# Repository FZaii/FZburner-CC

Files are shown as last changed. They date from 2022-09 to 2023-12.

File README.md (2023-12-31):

<p align="center">
  <a href="https://space.bilibili.com/1898517">
    
  </a>
    <br />
</p>

<h1 align="center">FZburner For CC</h1>

*<p align="center">给大鱼CC 3D打印机设计的一款打印头
  <br />
  [A burner for the DaYu CC 3D parinter]</p>*

**<p align="center">**
**<h3 align="center">最终版（v1.61）STEP及STL文件已上传！</h3>**
**<h3 align="center">✨[FZburner Mk2 已发布！！](https://github.com/FZaii/FZburner)✨</h3>**
*<p align="center">反馈意见可以通过[📺BiliBili](https://space.bilibili.com/1898517)私信</p>*

 ---
 
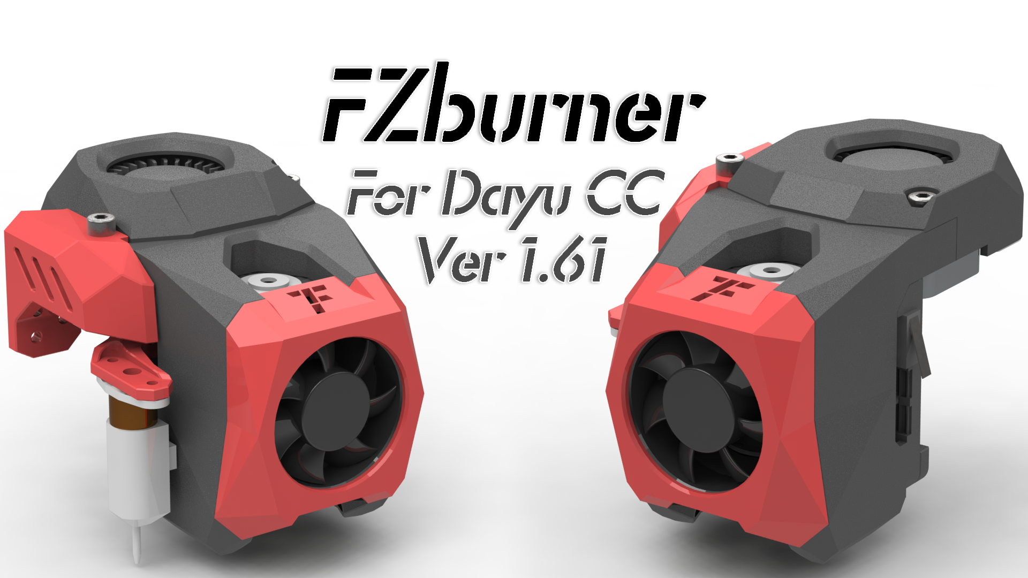
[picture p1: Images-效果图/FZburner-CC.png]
FZburner-CC

 
 ---

 ## 目录
 
- [功能特色](#功能特色)
- [更新历史](#更新历史)
- [实机照片](#实机照片)

 ---
  
### 功能特色
> - [x] 远程挤出（近程挤出可选用[**Sherpa Mini挤出机**](https://github.com/Annex-Engineering/Sherpa_Mini-Extruder)或者[**FZ挤出机**](https://github.com/FZaii/FZ-Extruder)等固定孔位间距为43.5mm的挤出机）
> - [x] E3D V6 热端
> - [x] 4010 热端风扇
> - [x] 4020 / 5015 物料风扇
> - [x] BLTouch 安装位
> - [x] [**Klicky/KlickyNG Probe**](https://github.com/jlas1/Klicky-Probe) / [**Euclid Probe**](https://github.com/nionio6915/Euclid_Probe)安装位
> - [x] ADXL345 安装位

### 更新历史

> **[Ver 1.61]** 2023.09.24
> - 优化“底板”，增加强度；
> - 新增“4B_5015物料风扇罩”等，以选装5015风扇;
> - 新增“7C_Euclid Probe支架”等，以选装Euclid Probe项目（PCB的klicky）;
> - 优化热端风扇罩，以安装36 PCB集线板（不支持36CAN板）
> - 最终版本，未来2.0再见！

> **[Ver 1.5]** 2022.11.19
> 
> **[Ver 1.4]** 2022.10.05
> 
> **[Ver 1.3]** 2022.09.11
> 
> **[Ver 1.2]** 2022.06.15
> 
> **[Ver 1.0]** 2022.04.30

### 实机照片

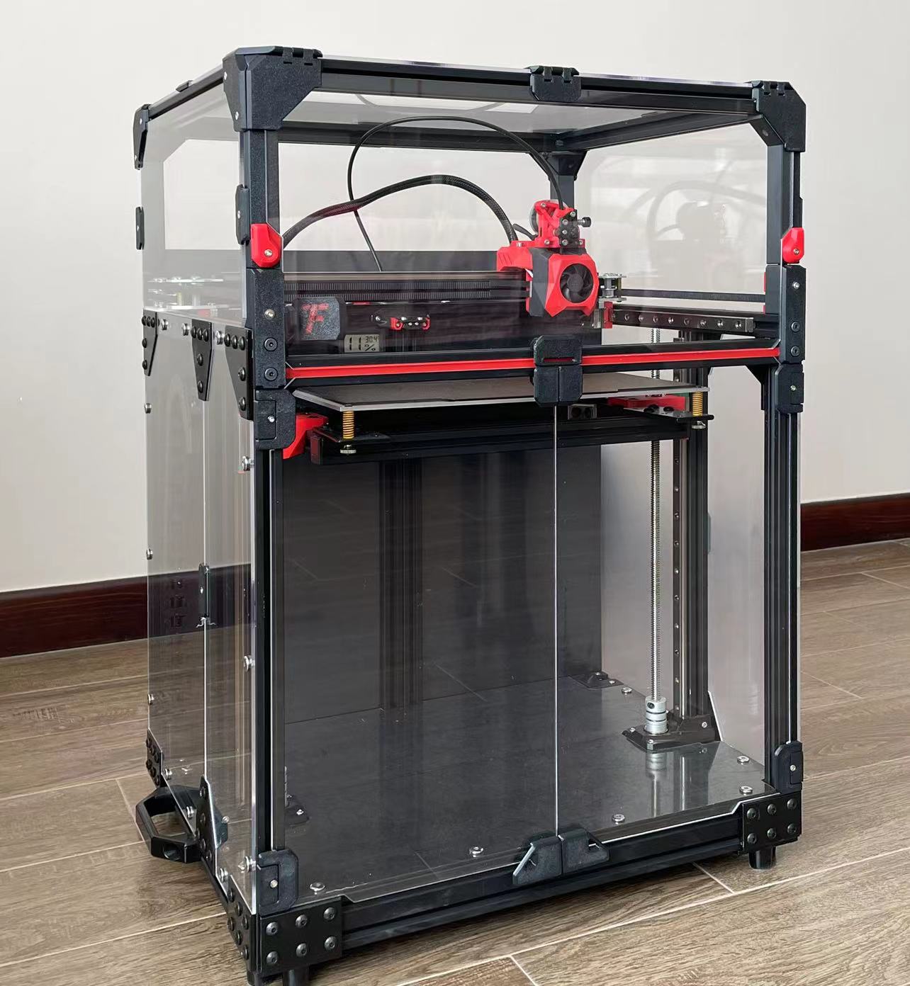
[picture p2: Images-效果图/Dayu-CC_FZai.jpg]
CC_FZai


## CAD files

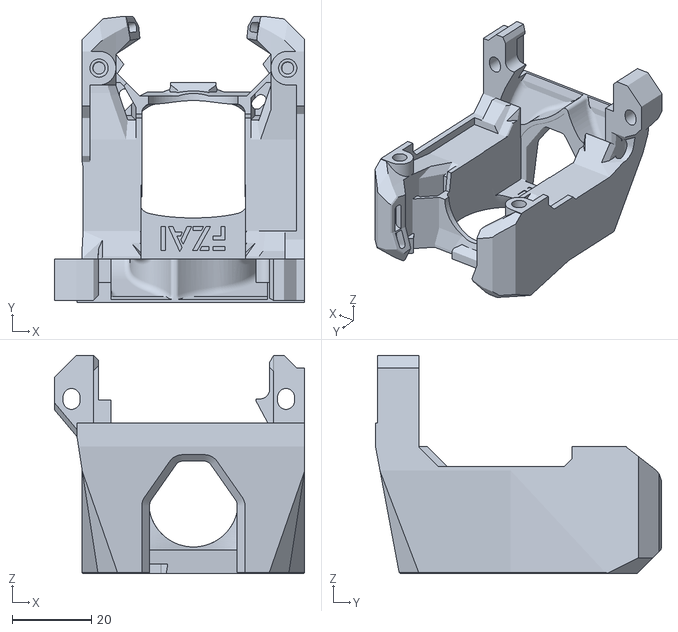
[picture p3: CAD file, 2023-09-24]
STLs-打印文件/可选换部件/3A_风道主体(远程)/3A_风道主体_main_body_ver1.61.STL
63.0 x 72.0 x 55.0

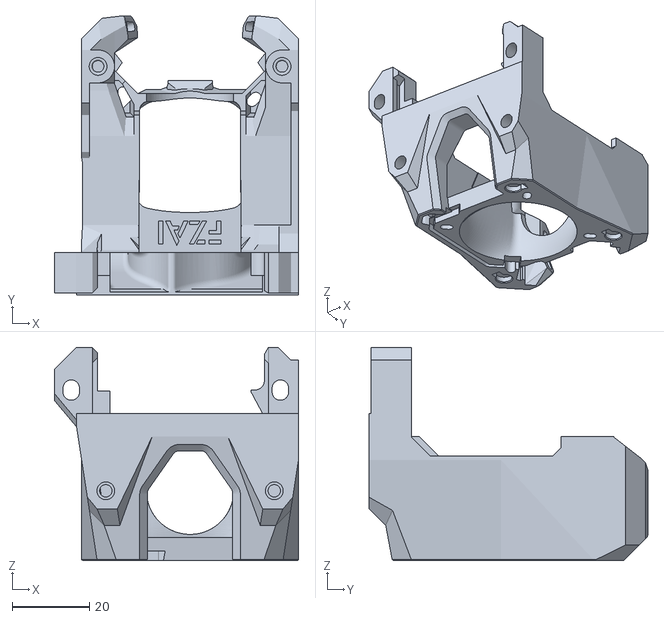
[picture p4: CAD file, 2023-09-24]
STLs-打印文件/3B_风道主体(近程)_main_body_(sherpa)_ver1.61.STL
63.0 x 72.0 x 55.0

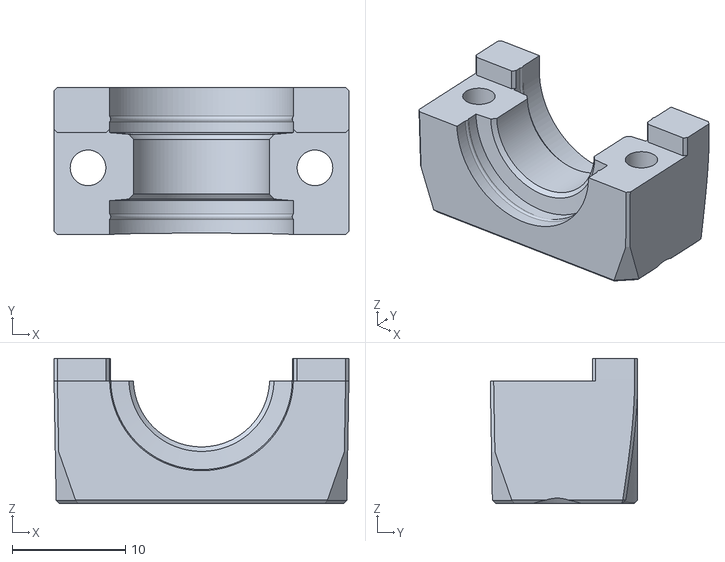
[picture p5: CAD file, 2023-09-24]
STLs-打印文件/2[1]_热端固定件_clamp_ver1.61.STL
26.0 x 13.0 x 12.8

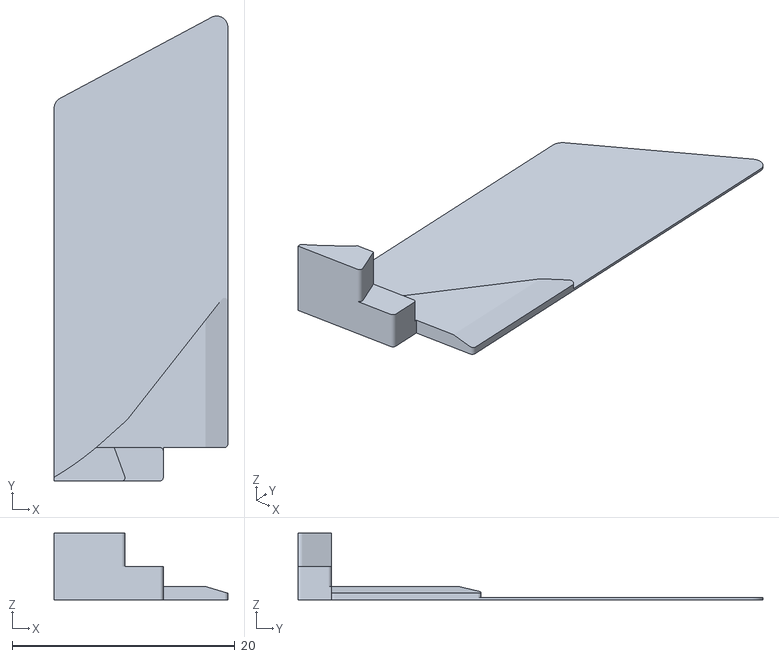
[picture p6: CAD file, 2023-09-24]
STLs-打印文件/可选换部件/4B_5015物料风扇/4B[2]_5015物料风扇补丁_5015Fan_patch_ver1.61.STL
15.6 x 41.7 x 6.00

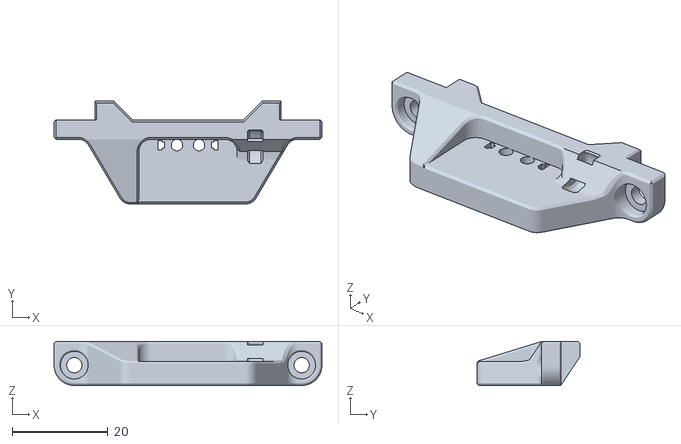
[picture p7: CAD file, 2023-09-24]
STLs-打印文件/可选换部件/7A_klicky/7A[1]_klicky支架_klicky_mount_ver1.61.STL
56.0 x 21.5 x 9.20

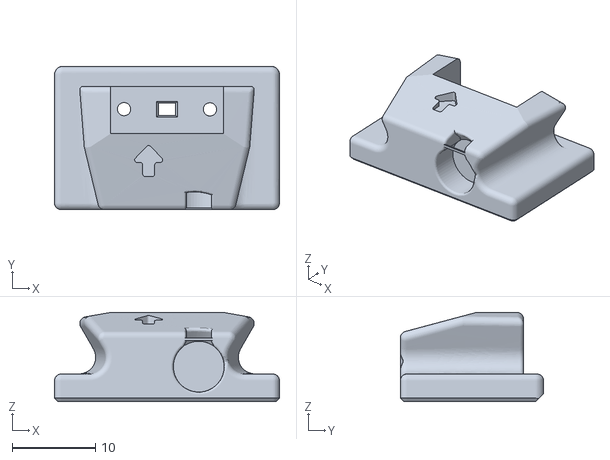
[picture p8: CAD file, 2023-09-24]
STLs-打印文件/可选换部件/7A_klicky/klicky_STL/KlickyProbe_v2.stl
27.0 x 17.2 x 10.7

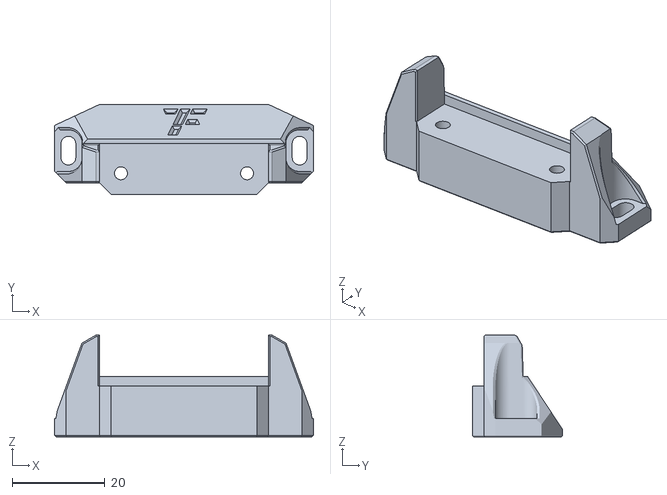
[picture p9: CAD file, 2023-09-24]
STLs-打印文件/可选换部件/7B_klickyNG/7B[3]_klickyNG停靠坞固定_klickyNG_Probe_Dock_mount_ver1.61.STL
56.0 x 19.5 x 22.0

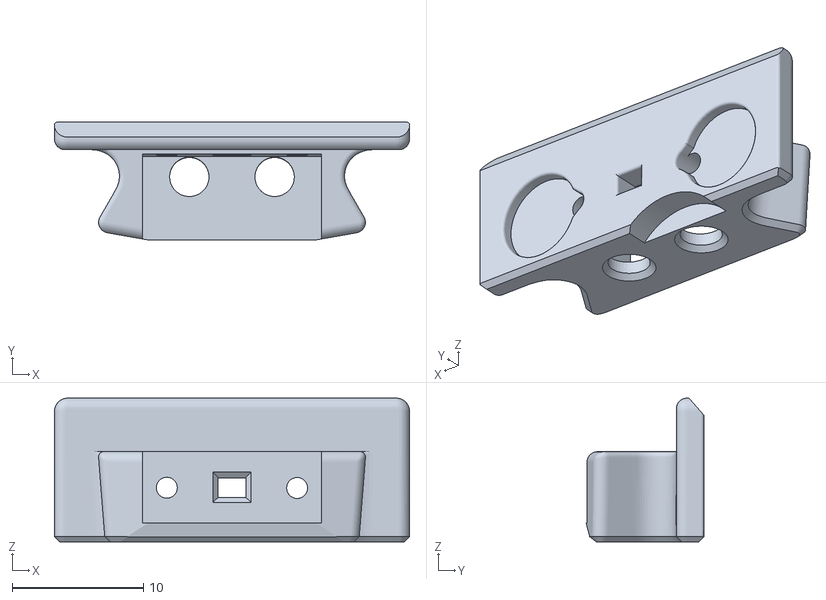
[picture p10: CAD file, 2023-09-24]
STLs-打印文件/可选换部件/7B_klickyNG/KlickyNG_STL/KlickyNG_Probe_insert_2_7mm.stl
27.0 x 8.97 x 10.9

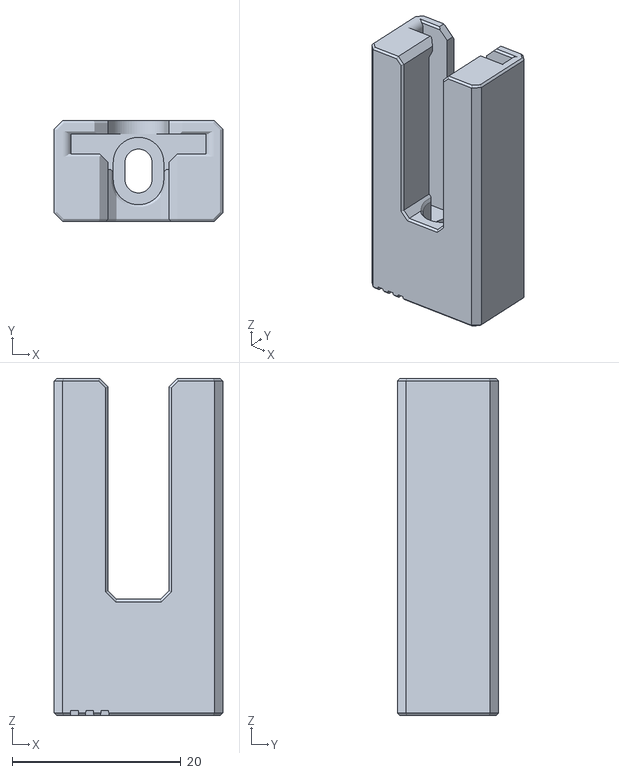
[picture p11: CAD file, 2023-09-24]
STLs-打印文件/可选换部件/7C_Euclid/7C[3]_Euclid停靠坞固定_Euclid_Dock_mount_ver1.61.STL
20.0 x 12.0 x 40.0

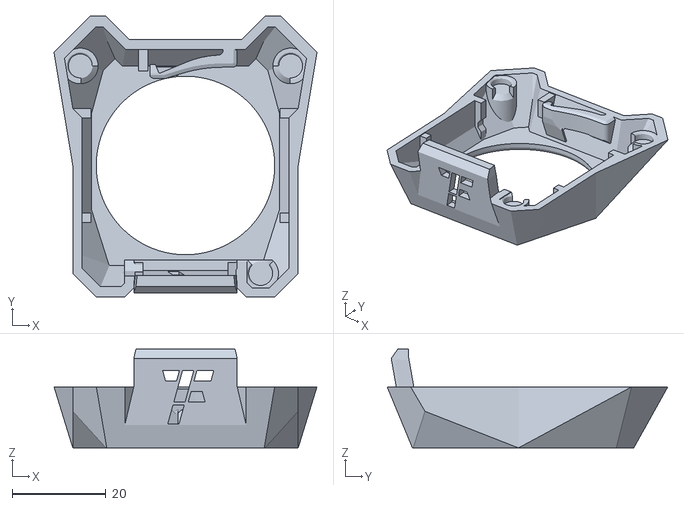
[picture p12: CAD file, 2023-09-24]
STLs-打印文件/5_4010热端风扇罩_4010Fan_cover_ver1.61.STL
56.0 x 59.8 x 21.0

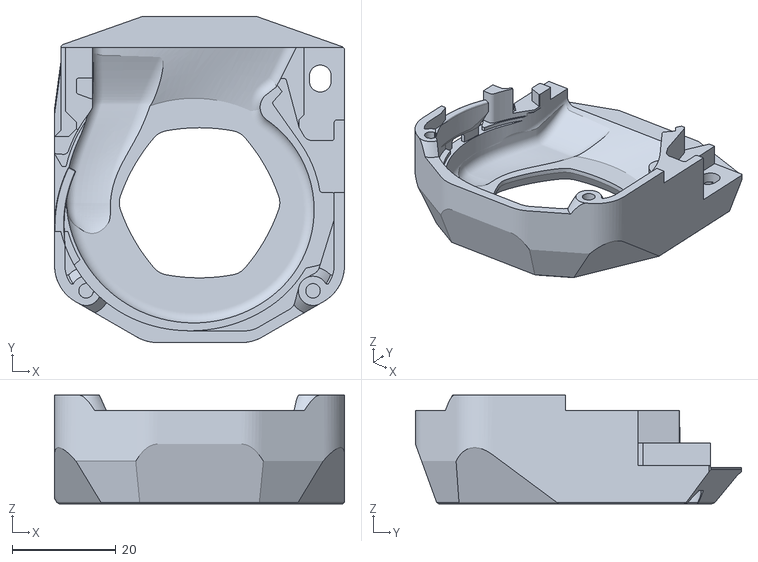
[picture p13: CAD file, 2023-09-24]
STLs-打印文件/可选换部件/4B_5015物料风扇/4B[1]_5015物料风扇罩_5015Fan_cover_ver1.61.STL
56.0 x 63.0 x 21.0

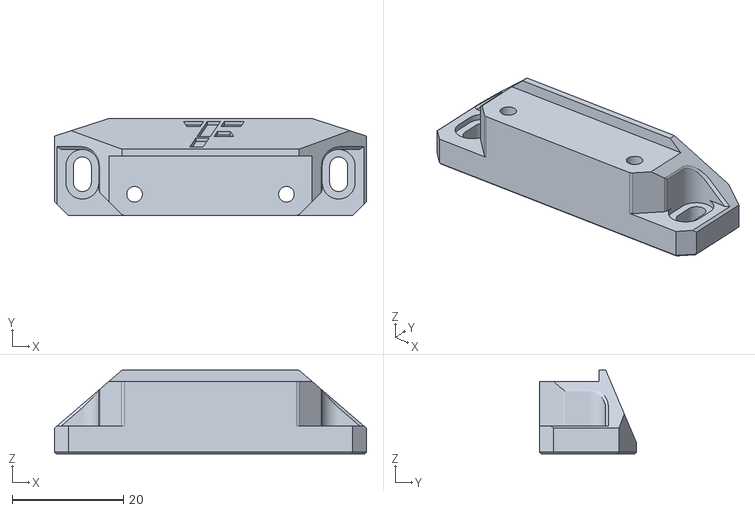
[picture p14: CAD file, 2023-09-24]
STLs-打印文件/可选换部件/7A_klicky/7A[2]_klicky停靠坞固定_klicky_Probe_Dock_mount_ver1.61.STL
56.0 x 17.4 x 15.0

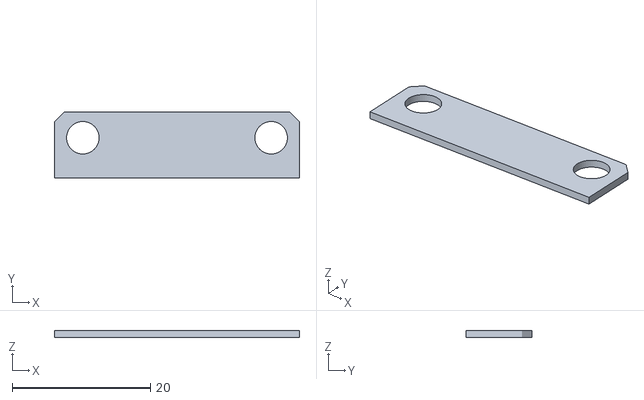
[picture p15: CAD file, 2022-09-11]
STLs-打印文件/可选换部件/7A_klicky/klicky_STL/1mm_Spacer.stl
35.5 x 9.50 x 1.00

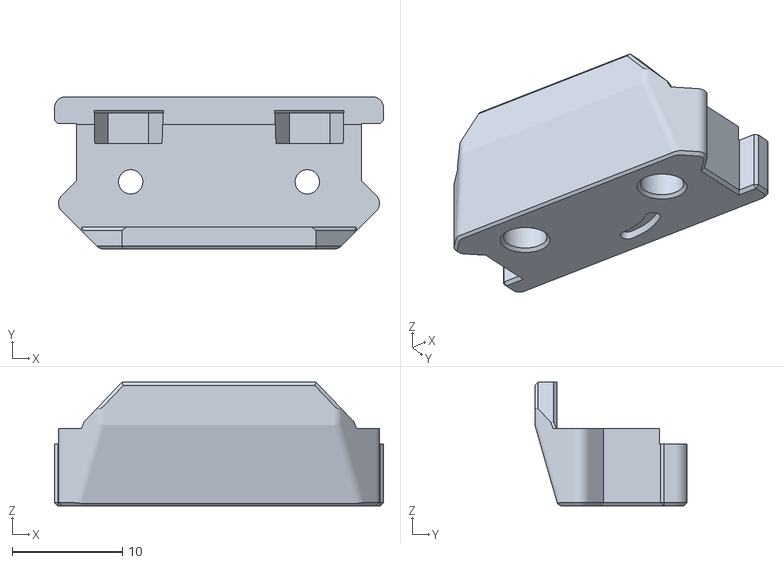
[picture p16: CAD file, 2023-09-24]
STLs-打印文件/可选换部件/7B_klickyNG/7B[2]_klickyNG支架_klickyNG_mount_ver1.61.STL
29.8 x 13.8 x 11.2

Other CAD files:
STLs-打印文件/可选换部件/2_热端固定件/2[2]_热端固定件_clamp_ver1.5.STL
STLs-打印文件/可选换部件/2_热端固定件/2[3]_热端固定件_clamp_ver1.5.STL
STLs-打印文件/可选换部件/7B_klickyNG/KlickyNG_STL/KlickyNG_Probe_body.stl
STLs-打印文件/可选换部件/7C_Euclid/7C[1]_Euclid支架_Euclid_mount_ver1.61.STL
STLs-打印文件/1_底板_rear_ver1.61.STL
STLs-打印文件/4A_4020物料风扇罩_4020Fan_cover_ver1.61.STL
STLs-打印文件/6_线缆罩_cable_cover_ver1.61.STL
STLs-打印文件/7D_ADXL345支架_FZburner_ADXL345_mount_ver1.61.STL
STLs-打印文件/8_BLTouch支架_FZburner_BLTouch_mount_ver1.61.STL
STLs-打印文件/可选换部件/2_热端固定件/2[0]_热端固定件_clamp_ver1.5.STL
STLs-打印文件/可选换部件/7A_klicky/klicky_STL/Probe_Dock_v2.1.stl
STLs-打印文件/可选换部件/7B_klickyNG/7B[1]_klickyNG支架_klickyNG_mount_ver1.61.STL
STLs-打印文件/可选换部件/7B_klickyNG/KlickyNG_STL/2mm_extender.stl
STLs-打印文件/可选换部件/7B_klickyNG/KlickyNG_STL/KlickyNG_Probe_Dock.stl
STLs-打印文件/可选换部件/7B_klickyNG/KlickyNG_STL/KlickyNG_Probe_insert_3mm.stl
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

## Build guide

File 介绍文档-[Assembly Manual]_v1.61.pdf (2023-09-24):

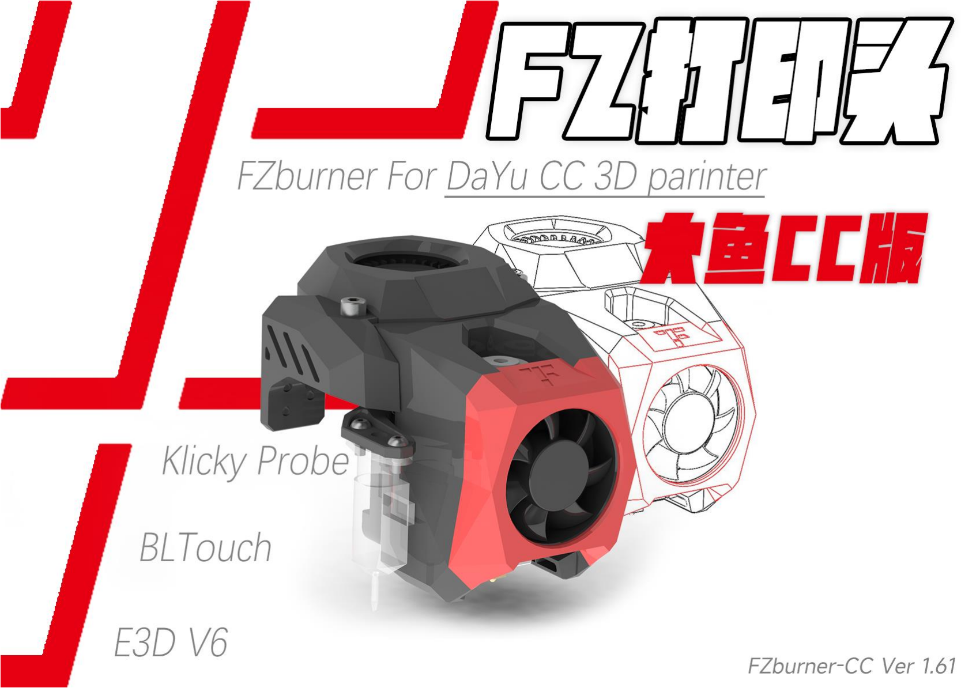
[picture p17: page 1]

FZburner-CC v1.61 | For DaYu CC 3D parinter

1

FZburner-CC v1.61 | For DaYu CC 3D parinter

1

# FZ 打印头 介绍文档

## [Assembly Manual]

所有件都可以无支撑打印，推荐参数：线宽 0.4mm，层高 0.2mm，轮廓 4， 顶层 4，底层 4。

## 打印件命名规则

4B[1]_5015 物料风扇罩_5015Fan_cover_ver1.61.STL

部件编号 款式 项目 | 名称 | 版本

Github 链接：（stl 和 step 文件）
链 接：https://github.com/FZaii/FZburner-CC

网 盘 链 接：（stl 文件）
链 接：https://pan.baidu.com/s/11pn74t0PChYZKoyyjINW8Q?pwd=utrv 提取码：utrv

## 物料清单 [BOM]

种类 | 型号 | 数量 | 使用位置
沉头内六角 (FHCS) | m3*30 | 2 | 热端固定件-2
半圆头内六角 (BHCS) | m3*8 | 5 | 同步带固定-2、BLtouch 固定-2、4020 风 扇固定-1
| m3*10 | 6 | 底板与 X 转接板-2、底板与主体-2(不安装 klicky 则用 m3x8)、4010 风扇固定-2
圆柱头内六角 (SHCS) | m4*16 | 2 | 主体与 X 转接板固定-2
| m2*8 | 3/7 | 限位开关-2、BLTouch 支架-1、 KlickyNG Probe-4
热熔螺母 (HEAT SET INSERT) | m3*5*4 | 4/6 | 底板-2、主体-2/4
圆柱磁铁 (Magnets) | 6*3 | 8 | Klicky Probe/ KlickyNG Probe
| 5*2 | 6 | 热端风扇罩固定 （最新版设计了卡扣，不需要此磁铁）

2

## 更新历史 [Update]

Version 1.61 2023-09-24
（1）优化“1_底板”，增加强度；
（2）新增“4B_5015 物料风扇罩”等，以选装 5015 风扇;
（3）新增“7C_Euclid Probe 支架”等，以选装 Euclid Probe 项目（PCB 的 klicky）; （4）优化热端风扇罩，以安装 36 PCB 集线板（不支持 36CAN 板） （5）最终版本，未来 2.0 再见！

Version 1.5 2022-11-19
（1）优化“1_底板”，以增加强度，更稳固的固定热端，简化限位开关走线； （2）优化“2[1]_热端固定件” ，以更稳固的固定热端；
（3）优化“3_风道主体” ，修改出风口角度，配合修改后的热端固定件及限位开关走线； （4）优化“5_4010 风扇罩” ，以增加风扇卡扣强度，配合修改后的风道主体； （5）优化“6_线缆罩” ，以改善打印件效果；
（6）优化“7[2]a_klicky 支架”、“9_ADXL345 支架” ，以配合修改后的底板外形； （7）新增“7[1]a_klickyNG 支架”等，以安装 Klicky NG 项目。

Version 1.4 2022-10-5
（1）“1.底板”增大了上下同步带的间距；
（2）“2."风道主体”出风口修改为常见的左右向后出风，优化 4010 风扇固定孔位及走线； （3）“4.热端风扇罩”修型。

Version 1.3 2022-9-11

Version 1.2 2022-6-15
（1）“2.风道主体” 改进了左右风道的风量分配，避免出风不同；顶部 4 个 M4 孔位。 （2）“1.底板”改进了热端固定位置，配合 4 个“3.x 热端固定件”可以实现热端的上下微调。 （3）“5.4020 涡轮风扇罩”改进了内部曲面，使空气流动更顺畅。

Version 1.0 2022-4-30
（1）重新设计了线缆走向，增加了“6.线缆罩-后出线带拖链”，将线缆引至打印头后方，可 以接 10*11 尼龙拖链，也可以直接扎带固定绕线管。
（2）“5.4020 涡轮风扇罩”内部增高 0.5mm，以适应不同品牌风扇，左侧孔位变动以配合线 缆罩。
（3）“1.底板-E3”封住了右侧用不上的 M2 螺丝孔位，没必要重打。

# 装配步骤

## [Steps]

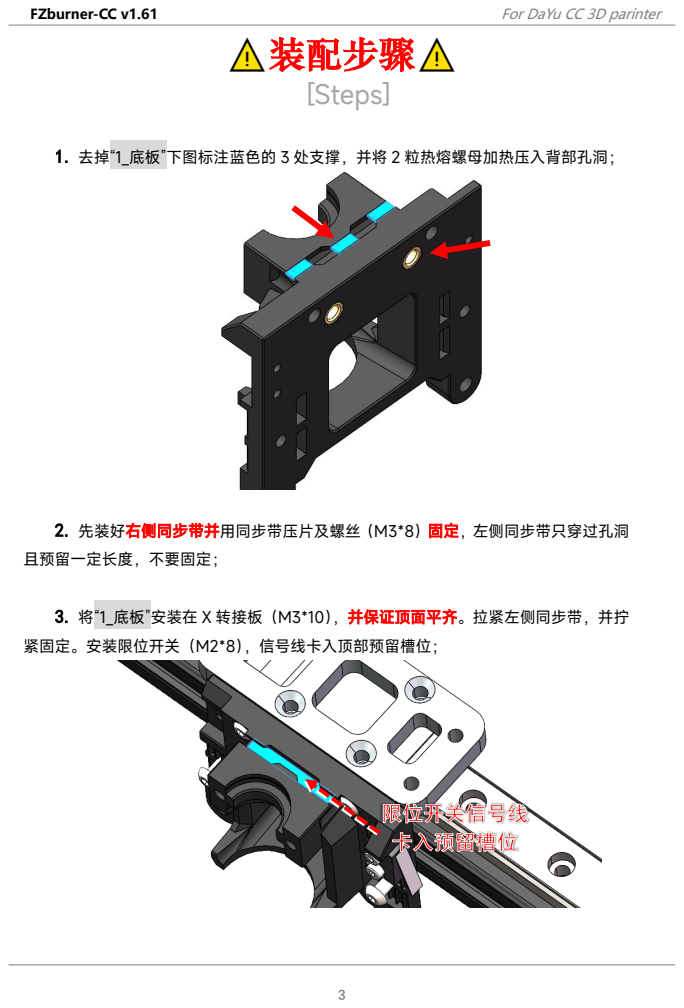
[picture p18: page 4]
且预留一定长度，不要固定；

1. 去掉“1_底板”下图标注蓝色的 3 处支撑，并将 2 粒热熔螺母加热压入背部孔洞；

2. 先装好右侧同步带并用同步带压片及螺丝（M3*8）固定，左侧同步带只穿过孔洞

3. 将“1_底板”安装在 X 转接板（M3*10），并保证顶面平齐。拉紧左侧同步带，并拧

紧固定。安装限位开关（M2*8），信号线卡入顶部预留槽位；

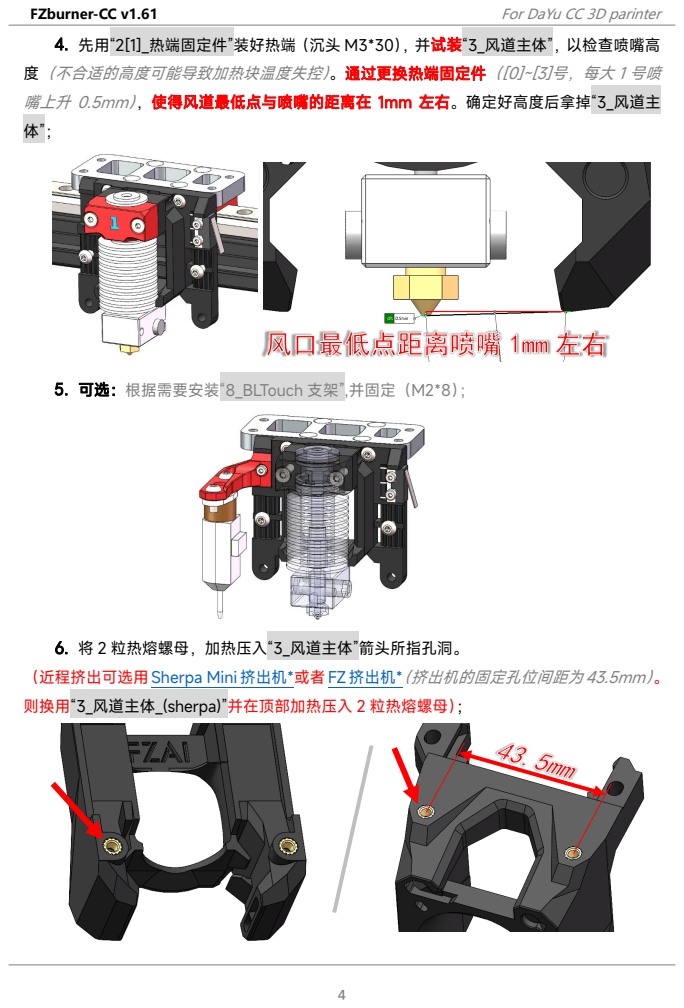
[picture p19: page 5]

4. 先用“2[1]_热端固定件”装好热端（沉头 M3*30），并试装“3_风道主体”，以检查喷嘴高

度（不合适的高度可能导致加热块温度失控）。通过更换热端固定件（[0]~[3]号，每大 1 号喷
嘴上升 0.5mm），使得风道最低点与喷嘴的距离在 1mm 左右。确定好高度后拿掉“3_风道主

5. 可选：根据需要安装“8_BLTouch 支架”,并固定（M2*8）；

6. 将 2 粒热熔螺母，加热压入“3_风道主体”箭头所指孔洞。

（近程挤出可选用Sherpa Mini挤出机*或者 (https://github.com/Annex-Engineering/Sherpa_Mini-Extruder)FZ挤出机（* (https://github.com/FZaii/FZ-Extruder) 挤出机的固定孔位间距为43.5mm）。
则换用“3_风道主体_(sherpa)”并在顶部加热压入 2 粒热熔螺母）；

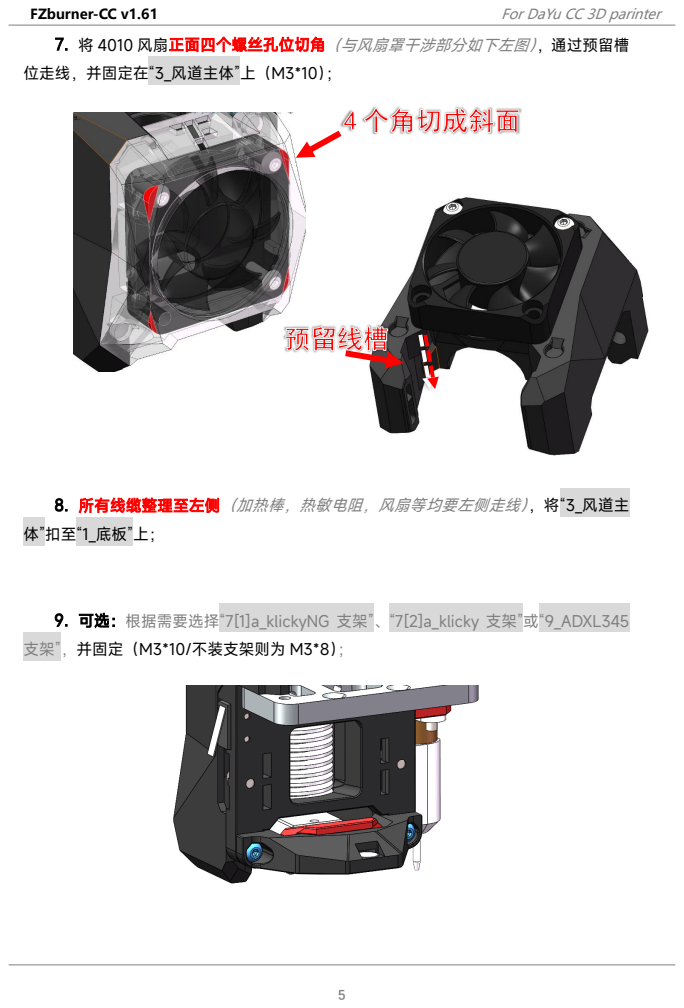
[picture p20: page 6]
位走线，并固定在“3_风道主体”上（M3*10）；

7. 将 4010 风扇正面四个螺丝孔位切角（与风扇罩干涉部分如下左图），通过预留槽

8. 所有线缆整理至左侧（加热棒，热敏电阻，风扇等均要左侧走线），将“3_风道主

9. 可选：根据需要选择“7[1]a_klickyNG 支架”、“7[2]a_klicky 支架”或“9_ADXL345

支架”，并固定（M3*10/不装支架则为 M3*8）；

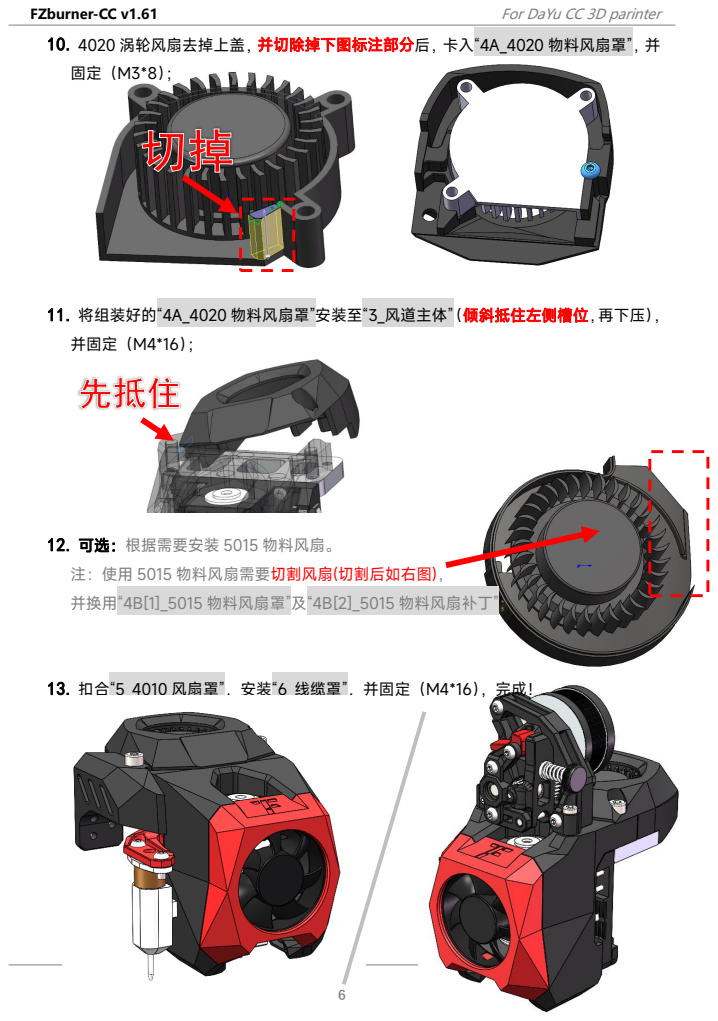
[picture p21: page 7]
并固定（M4*16）；

10. 4020 涡轮风扇去掉上盖，并切除掉下图标注部分后，卡入“4A_4020 物料风扇罩”，并

11. 将组装好的“4A_4020 物料风扇罩”安装至“3_风道主体”（倾斜抵住左侧槽位，再下压），

12. 可选：根据需要安装 5015 物料风扇。

注：使用 5015 物料风扇需要切割风扇(切割后如右图)，
并换用“4B[1]_5015 物料风扇罩”及“4B[2]_5015 物料风扇补丁”；

13. 扣合“5_4010 风扇罩”，安装“6_线缆罩”，并固定（M4*16），完成！

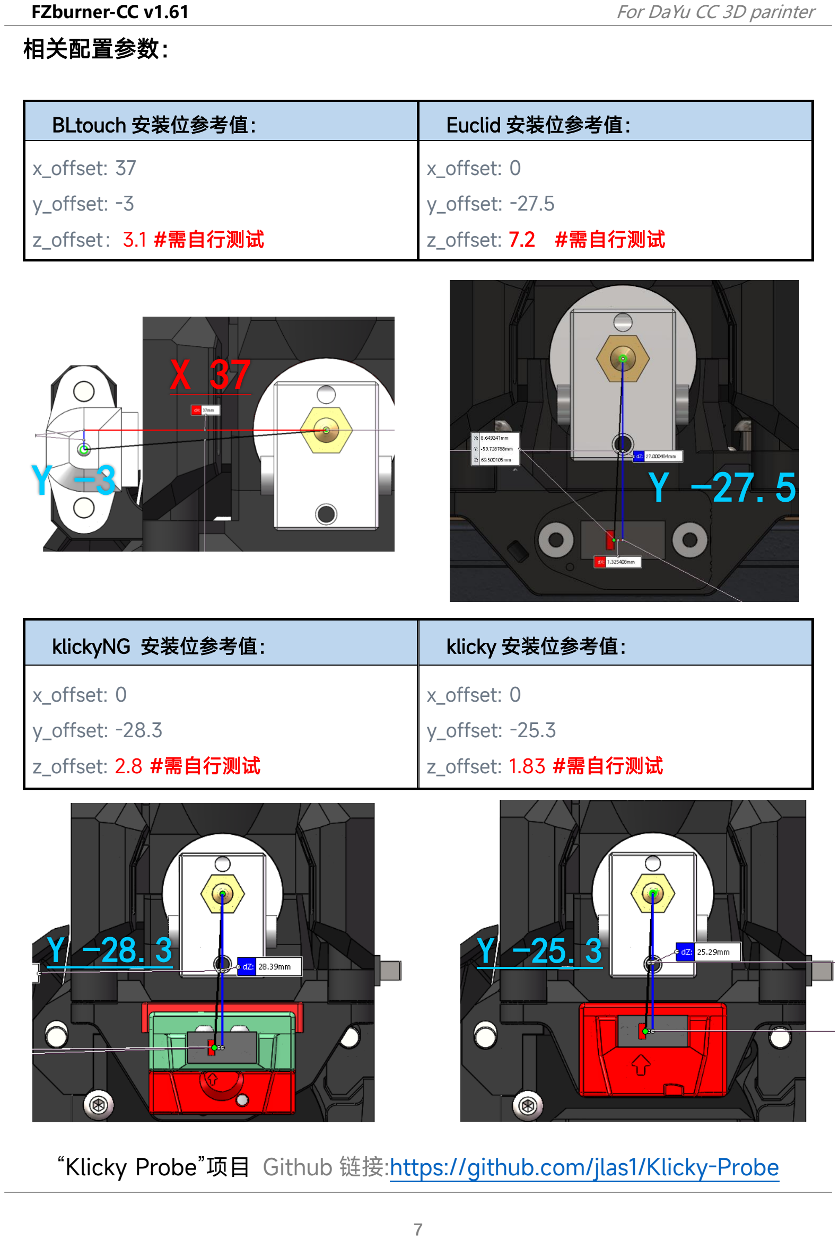
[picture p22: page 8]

7

相关配置参数：

BLtouch 安装位参考值： | Euclid 安装位参考值：
x_offset: 37 y_offset: -3 z_offset：3.1 #需自行测试 | x_offset: 0 y_offset: -27.5 z_offset: 7.2 #需自行测试
klickyNG 安装位参考值： | klicky 安装位参考值：
x_offset: 0 y_offset: -28.3 z_offset: 2.8 #需自行测试 | x_offset: 0 y_offset: -25.3 z_offset: 1.83 #需自行测试

“Klicky Probe”项目 Github 链接:https://github.com/jlas1/Klicky-Probe

X 37

Y -3

Y -28.3 | Y -25.3

Y -27.5
